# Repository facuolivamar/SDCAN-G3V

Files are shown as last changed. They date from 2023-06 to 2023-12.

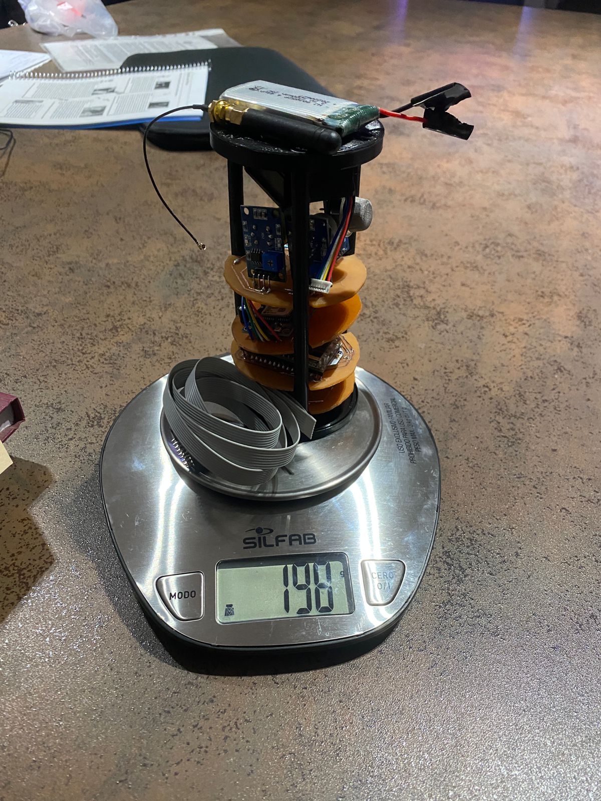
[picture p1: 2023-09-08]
Multimedia/balanza.jpeg

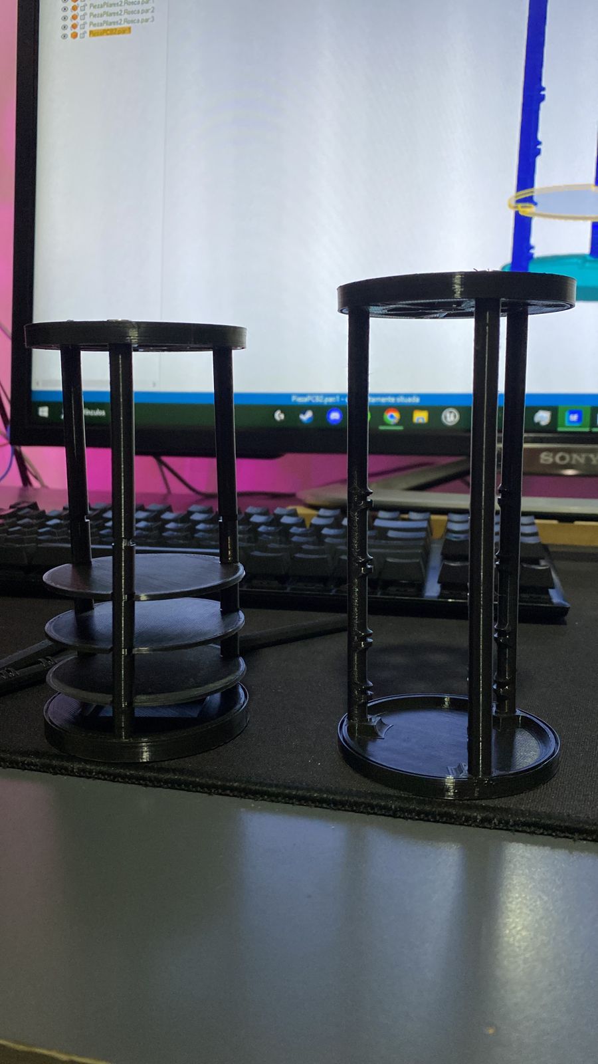
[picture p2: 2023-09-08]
Multimedia/produccion-estructura.jpeg

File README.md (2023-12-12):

# Smog Detector CAN (SDCAN)

## Introduction
This readme provides an overview of the SDCAN project developed by the Equipo Villada para la Investigación Espacial (EVIE) from Instituto Técnico Salesiano Villada. The project aims to measure and monitor air pollution levels in the province of Córdoba, Argentina, using a CanSat (Satellite in a Can) device. The CanSat will collect data on pressure, temperature, ozone levels, nitrogen oxides, volatile organic compounds, carbon dioxide, and particulate matter. The project's primary mission is to transmit this data to a ground station in real-time, while the secondary mission involves studying pollution levels in different areas of the province.

## Mission Name: SDCAN (Smog Detector CAN)
Patch:
Team Organization: Roles
- Luciano Michalik - Teacher Advisor
- Maximiliano Smidt – Structure Designer
- Valentino Velez – Hardware and Firmware Developer
- Facundo Oliva Marchetto – Software Developer
- Mateo Marchisone – Software Developer and Outreach

## Mission Objectives
Primary Mission:
The primary mission consists of sensing pressure and temperature and transmitting this data to the ground station at least once per second. The initial data obtained from measuring pressure and temperature before launch will be used to calculate the CANSAT's altitude, which will be utilized in the secondary mission.

Secondary Mission:
The secondary mission involves studying pollution levels based on the following factors:
- Topography of Córdoba: The city's topography, combined with the phenomenon of thermal inversion, leads to the accumulation of pollutants near the ground, resulting in the formation of a smog cloud.
- Levels of nitrogen oxides in the Province of Córdoba: The high concentration of vehicles and industrial activities, particularly in the automotive and agricultural sectors, contributes to elevated levels of nitrogen oxides (NOx).
- Levels of volatile organic compounds in the Province of Córdoba: Agricultural and livestock activities, along with industrial processes, generate high levels of volatile organic compounds (VOCs) such as methane, toluene, and ethylene.
- Particulate matter 2.5 PM: Fine particulate matter with a diameter of 2.5 microns (PM2.5), originating from various sources, poses health and environmental risks.

The mission aims to measure air quality, NOx levels, VOCs, ozone (O3), and carbon dioxide (CO2) in different areas of the province, including industrial parks and agricultural zones, complementing the existing air quality monitoring stations in the city of Córdoba.

## Preliminary Design
Physical Layout:
The CANSAT's behavior during the mission will follow these steps:
1. While loaded into the rocket before launch, the CANSAT will remain in a dormant state to conserve energy.
2. Once in flight, the CANSAT will start recording all data.
3. Upon ejection, the CANSAT will initiate data transmission while continuing to gather more information.
4. During freefall descent, the parachute will deploy, ensuring a controlled landing.

Subsystems:
- Microprocessor (Computer): The ESP32-LoRa provided by CONAE will be used to store and transmit data, as well as read and process various sensor measurements.
- Communications: The LoRa module integrated into the ESP32 will enable long-range and low-energy data transmission.
- Sensors:
  - Ozone and nitrogen dioxide sensor (MQ131): Used to measure ozone (O3) and nitrogen oxides (NOx) levels.
  - LPG, methane, and carbon monoxide sensor (MQ4): Measures LPG, methane, and CO levels.
  - Air quality sensor (MQ135): Measures CO2, benzene, and toluene levels.
  - GPS module (GY-NEO6MV2): Provides real-time location coordinates.
  - Dust and particle sensor (GP2Y1010AU0F): Measures 2.5 PM particles in the air.
  - NH3 and NO2 sensor (Mics 6814): Measures ammonia and nitrogen dioxide levels.

- Power Unit: A 3.7V, 1200mAh lithium battery will be used as the power source. Voltage regulators (step-up and step-down) will be employed to supply the required voltages (3.3V and 5V) to different components.

## Budget of Mass
The estimated total mass of the CANSAT is 239.45 grams.

## Integration and Testing
The components will undergo preliminary individual testing before the CANSAT assembly. Integration tests will include parachute functionality, descent control, and data transmission. Additionally, the CANSAT will be subjected to simulated conditions such as vacuum and vibration tests to ensure its integrity.

## Documentation and Results
The project's progress will be documented using GitHub for version control. Various documents will outline each stage of the project. Videos and photos will be taken to capture key milestones. Results will be shared through a YouTube channel and an Instagram account dedicated to the project.

GitHub Repository: [Project Repository](https://github.com/facuolivamar/SDCAN-G3V/tree/main)

YouTube Channel: [EVIE SDCAN](https://www.youtube.com/@ITSV-SDCAN)

Instagram Account: [@sdcan_itsv](https://www.instagram.com/sdcan_itsv/)

For a detailed description and visual representation of the project, please refer to the [project video](https://www.youtube.com/watch?v=PZLdEqGG1FY&ab_channel=ITSV-SDCAN).

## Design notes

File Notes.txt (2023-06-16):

Instalar driver para USB
Instalar zip library > SFE_BMP180-master.zip
1. Resistencias
2. Version de la libreria, Version: BPM085 1.0.0
examples >  adafruit BPM085 library > test
examples > WireScan

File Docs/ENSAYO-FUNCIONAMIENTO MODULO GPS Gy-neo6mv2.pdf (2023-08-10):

ENSAYO: Funcionamiento del Módulo GPS Gy-neo6mv2.

En este ensayo, se buscó comprobar el correcto funcionamiento de Módulo GPS Gy-neo6mv2. Para ello, Se utilizo la librería TinyGPS++ y se comprobó que los datos de latitud y longitud que estaba arrojando el sensor sean correctos con la ubicación donde estaba el dispositivo.

Materiales utilizados

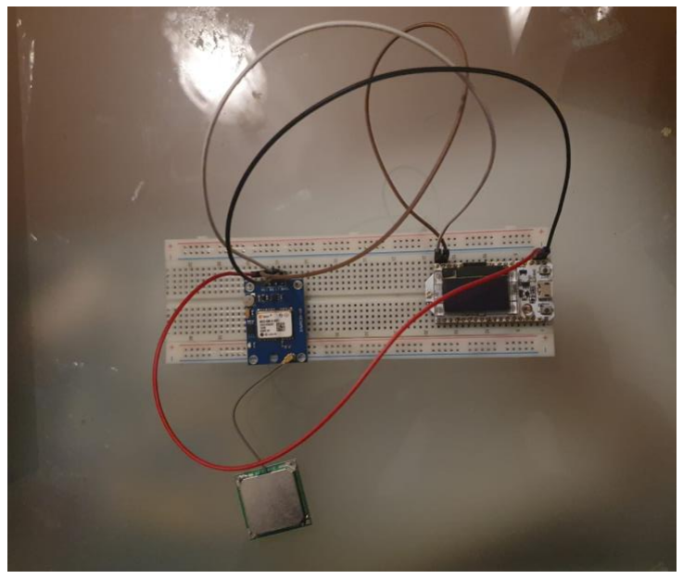
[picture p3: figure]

- WiFi LoRa 32 (V2)
- Módulo GPS Gy-neo6mv2
- Protoboard
- Cables Dupont Macho-Macho

Resultados obtenidos:

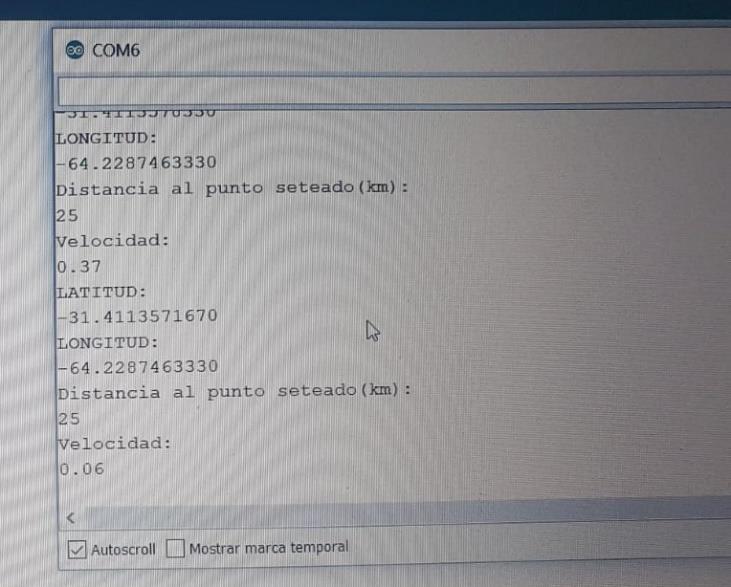
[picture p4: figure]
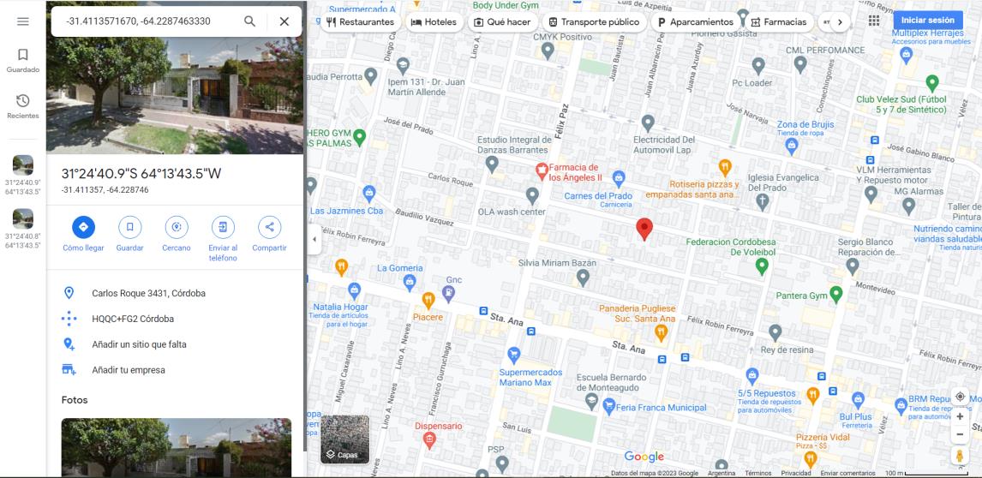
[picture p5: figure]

Los valores de latitud y longitud arrojados por el modulo fueron puestos en Google maps para corroborar que la información que estába dando era correcta.

Conclusiones

- Gracias a los resultados obtenidos se puede preveer el correcto funcionamiento del dispositivo para nuestra misión.

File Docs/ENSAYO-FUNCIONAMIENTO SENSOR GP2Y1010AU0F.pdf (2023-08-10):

ENSAYO: Funcionamiento del Sensor GP2Y1010AU0F

En este ensayo, se busco comprobar el correcto funcionamiento del sensor GP2Y1010AU0F. Para ello, se realizaron pruebas con fósforos con la finalidad de comprobar que el sensor sea capaz de medir la densidad de partículas que desprendían las cerillas al ser apagadas.

Materiales utilizados

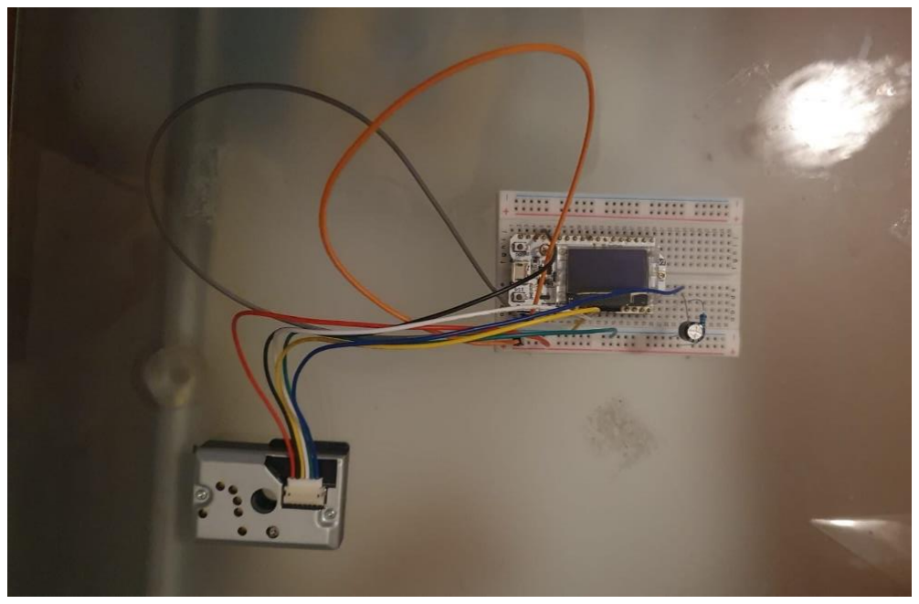
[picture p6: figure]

- WiFi LoRa 32 (V2)
- Sensor GP2Y1010AU0F
- Protoboard
- Resistencia 150 Ω
- Capacitor 220 µF
- Cables Dupont Macho-Macho

Condiciones iniciales:

- Se efectuó 3 testeos en un ambiente cerrado
- Las cerillas fueron apagadas lo más cerca posible del sensor.

Resultados obtenidos:

Conclusiones

- Dado las condiciones del ensayo (ambiente cerrado, sin circulación de aire) se obtuvieron resultados bastantes congruentes entre sí, con una precisión del 1,70%.
- Gracias a los resultados obtenidos se puede preveer el correcto funcionamiento del dispositivo para nuestra misión.
| Valor medio
Valor inicial
| obtenido
(ug/m3)
| (ug/m3)
0 | 2699,00
0 | 2673,00
0 | 2611,00
Precisión | 45,21
Precisión porcentaje | 1,70%

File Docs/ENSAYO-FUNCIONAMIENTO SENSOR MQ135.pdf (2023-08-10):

ENSAYO: Funcionamiento del Sensor MQ135

En este ensayo, se buscó comprobar el correcto funcionamiento del sensor MQ135. Para ello, se realizaron pruebas para corroborar si el sensor MQ135 era capaz de sensar compuestos orgánicos volátiles (benceno, tolueno) siendo útil para nuestra misión. Para ello, se utilizó alcohol y un esmalte de uñas (el esmalte de uñas está compuesto internamente por tolueno)

Materiales utilizados

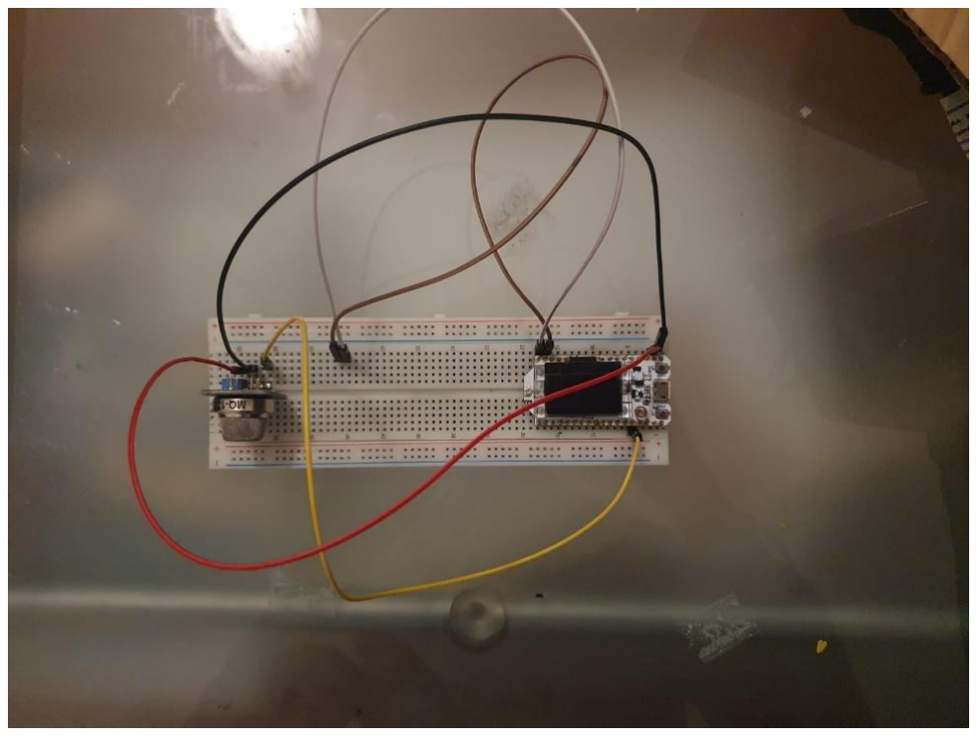
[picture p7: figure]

- WiFi LoRa 32 (V2)
- Sensor MQ135
- Protoboard
- Cables Dupont Macho-Macho

Condiciones iniciales:

- Se efectuó 3 testeos con una tapita llena de alcohol en un ambiente cerrado
- Se efectuó 3 testeos con un esmalte de uñas en un ambiente cerrado.

- El alcohol y el esmalte de uñas fueron puestos lo más cerca posible del sensor

Resultados obtenidos:

Precisión | 10,60
Precisión porcentaje | 12,71%

Conclusiones

- Al ser expuesto al alcohol se obtuvieron resultados bastantes congruentes entre sí, con una precisión del 2,15%.
- Al ser expuesto al esmalte de uñas se obtuvieron resultados bastantes congruentes entre sí, con una precisión del 12,71%.
- Gracias a los resultados obtenidos se puede preveer el correcto funcionamiento del dispositivo para nuestra misión.

Valor inicial alcohol
(ppm)

Valor máx obtenido
despues de 20
segundos expuesto al
alcohol (ppm)
0,09 | 122,28
0,54 | 117,37
0,06 | 121,21
Precisión | 2,58
Precisión porcentaje | 2,15%

Valor inicial tolueno
(ppm)

Valor máx obtenido
despues de 20
segundos expuesto al
tolueno (ppm)
0.10 | 89,42
0.14 | 89,7
0,06 | 71,2

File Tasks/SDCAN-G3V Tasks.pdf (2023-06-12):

Date | Task | Description | Status
23/06/2023 | Primera revisión crítica | Video de la misión primaria, la estructura y el sistema de descenso. Desarrollar sistema para la realizacion de la mision primaria.
23/06/2023 | Estacion espacial | Sensado de presión y temperatura y la transmisión de esos datos a la estación terrena al menos una vez por segundo. (Microprocesador ESP32-LoRa, Sensor MBP180, antena, Batería necesaria, etc)
23/06/2023 | Estacion terrena | Recibir datos de estacion espacial.
23/06/2023 | Interfaz Front-End | Leer desde el puerto serial todos los datos recopilados por el CANSAT y guardar estos datos en un archivo .CSV, además de mostrar valores de interés tales como nivel de batería, posición, etc.
23/06/2023 | Estructura | Estructura en impresion 3D.
23/06/2023 | Sistema de descenso | Paracaídas y electrónica necesaria del mismo. Desarrollar sistema para aterrizaje controlado (GPS, cebos, etc).
23/06/2023 | Video de la mision primaria | Video de funcionamiento de todo lo trabajado en esta primera etapa(mision primaria).

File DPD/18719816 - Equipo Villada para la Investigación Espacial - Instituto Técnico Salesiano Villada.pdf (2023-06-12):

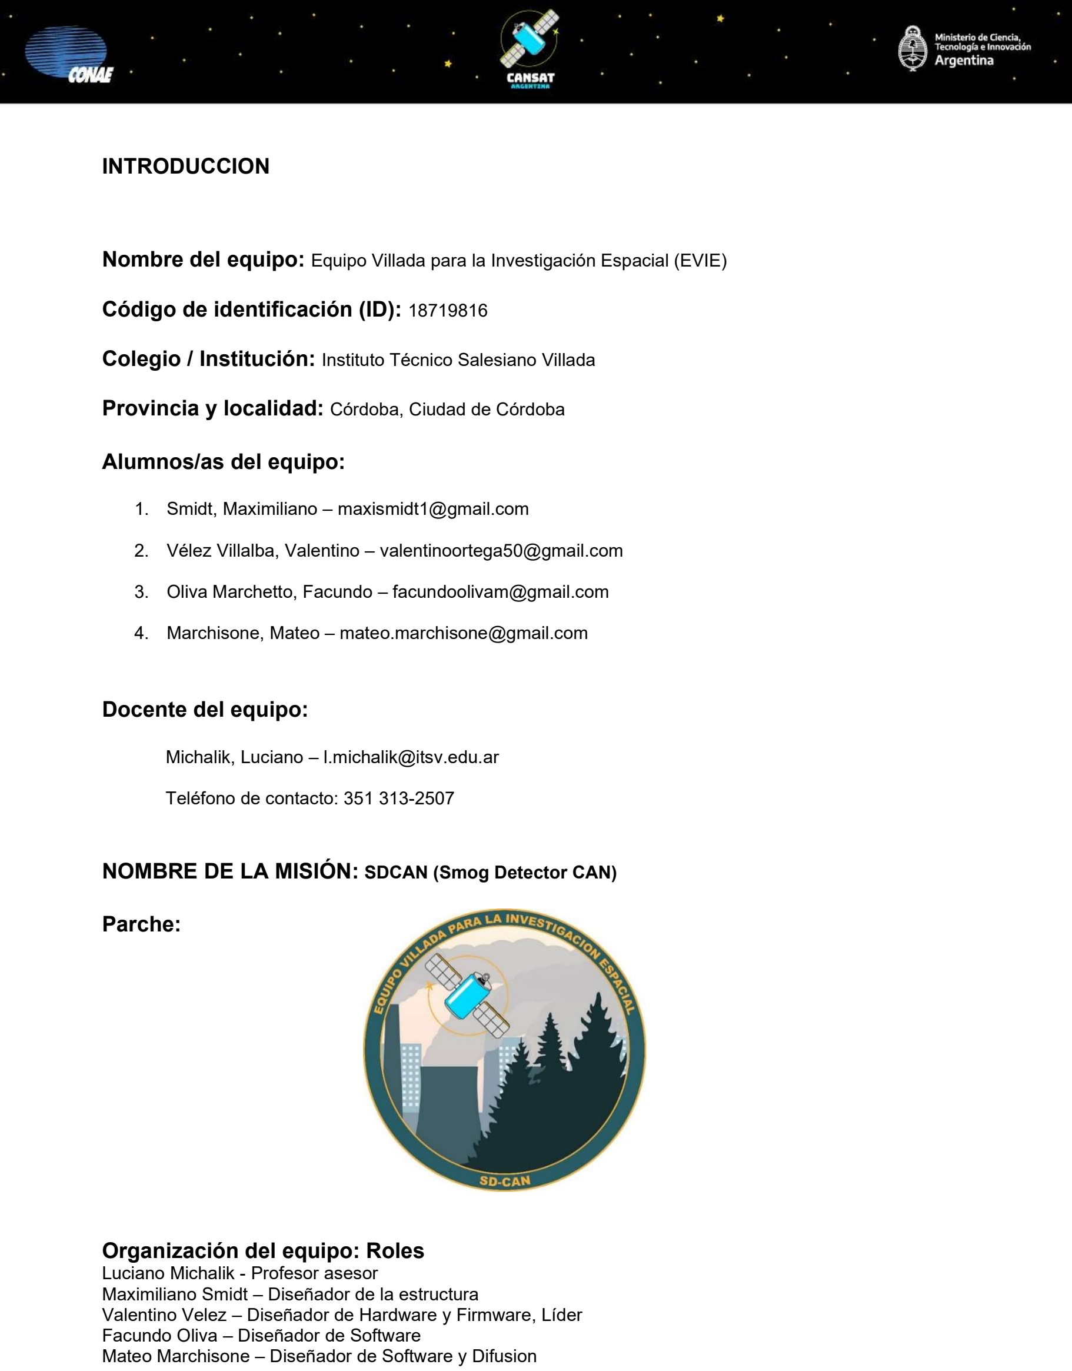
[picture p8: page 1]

### INTRODUCCION

Nombre del equipo: Equipo Villada para la Investigación Espacial (EVIE)

### Código de identificación (ID): 18719816

Colegio / Institución: Instituto Técnico Salesiano Villada

Provincia y localidad: Córdoba, Ciudad de Córdoba

### Alumnos/as del equipo:

### 1. Smidt, Maximiliano – maxismidt1@gmail.com

### 2. Vélez Villalba, Valentino – valentinoortega50@gmail.com

### 3. Oliva Marchetto, Facundo – facundoolivam@gmail.com

### 4. Marchisone, Mateo – mateo.marchisone@gmail.com

### Docente del equipo:

Michalik, Luciano – l.michalik@itsv.edu.ar

Teléfono de contacto: 351 313-2507

NOMBRE DE LA MISIÓN: SDCAN (Smog Detector CAN)

### Parche:

### Organización del equipo: Roles

Luciano Michalik - Profesor asesor
Maximiliano Smidt – Diseñador de la estructura
Valentino Velez – Diseñador de Hardware y Firmware, Líder Facundo Oliva – Diseñador de Software
Mateo Marchisone – Diseñador de Software y Difusion

2

OBJETIVOS DE LA MISIÓN….

### Misión primaria

La misión primaria consiste en el sensado de presión y temperatura y la transmisión de esos datos a la estación terrena al menos una vez por segundo
Para el cálculo de altura del CANSAT, se medirán la presión y temperatura antes del despegue y de esa manera conseguir los datos iniciales necesarios para el cálculo. Este dato lo utilizaremos posteriormente para la misión secundaria

### Misión secundaria

Para la misión secundaria, se realizó un estudio de los niveles de contaminación en base a los siguientes puntos.

### Topografía de Córdoba

En los días de invierno, se produce en la ciudad de Córdoba el fenómeno llamado inversión térmica. Tiene origen en el enfriamiento nocturno del suelo que hace descender la temperatura del aire próximo, que, por ser más pesado, queda estacionado abajo, hasta que, por irradiación solar, se calienta y asciende. Lo que produce la acumulación de contaminantes a pocos metros del suelo y permite que se combinen con la neblina generando así lo que se denomina “nube de smog”
Particularmente dada a la topografía de la ciudad dicho smog es altamente nocivo, ya que la ciudad está en un valle que corre de oeste a este, lo que limita el ‘barrido’ de los vientos norte y sur. Córdoba se ubica en una depresión, por lo cual la circulación y remoción del aire es mucho más lenta.

### Valores de óxidos de nitrógeno en la Provincia de Córdoba

Después de la provincia de Buenos Aires, Córdoba, es la segunda provincia con el mayor número de vehículos en el país (1,49 millones de vehículos)
Industrialmente, Córdoba concentra el 30% de la producción automotriz nacional. En la provincia están instaladas plantas terminales de importantes automotrices mundiales: FCA, Renault, Volkswagen, IVECO y Nissan. Cuenta con una muy desarrollada red de medianas y pequeñas industrias metalmecánicas.
Otro polo industrial es el sector de fabricantes de bienes de capital agrícola, en especial maquinarias y agro componentes.
Además, posee 45 Parques Industriales habilitados, de los cuales, la mayoría están ubicados en la zona sudeste de la región.
Estos factores generan altos niveles de óxidos de nitrógeno, los cuales son unos de los químicos presentes en el smog. Se originan como consecuencia de las combustiones de quemadores, a partir del tráfico y de procesos industriales.

Valores de compuestos orgánicos volátiles en la Provincia de Córdoba.
En temas de agronomía, las principales producciones de Córdoba son las de trigo, maíz, sorgo, soja, girasol y maní.
En actividad ganadera, es la segunda provincia a nivel nacional después de la provincia de Buenos Aires. Su principal producción es el ganado bovino, seguido del porcino, caprino y ovino.
Estos factores generan altos niveles de compuestos orgánicos volátiles (COVs), los cuales son unos de los químicos presentes en el smog. Tienen un origen tanto natural (por el ganado y la agricultura) como antropogénico (debido a la evaporación de disolventes orgánicos, a la quema de combustibles, al transporte, etc.). Si bien hay millones de compuestos que pueden considerarse como COV; los más abundantes son: metano, tolueno, n-butano, i-pentano, etano, benceno, n-pentano, propano y etileno.

### Material particulado 2,5 PM

El material particulado de 2,5 micrones (PM2,5) es tan pequeño que puede inhalarse al respirar y se puede alojar directamente en los pulmones con la posibilidad de que llegue al torrente sanguíneo. Procede de distintas fuentes, en especial por la combustión de combustibles fósiles (tráfico, calefacción, generación de energía), minería, actividades de construcción y demolición o incendios, los cuales pueden generar este tipo de contaminación porque producen partículas livianas que pueden llegar a las ciudades por el viento.

3

Valores del dióxido de carbono en la Provincia de Córdoba.
Además de medir los valores previamente escritos, vamos a medir los niveles de dióxido de carbono (CO2). Las emisiones excesivas de este gas son una de las principales causas del calentamiento global. Un problema causado por la actividad humana, proveniente del consumo energético de los edificios, el transporte y por residuos y cloacas.
Según un dato de la municipalidad del año 2017, la ciudad de Córdoba emite 5,1 millones de toneladas de dióxido de carbono (CO2) al año.

### Daños a la salud y al medioambiente

Algunos de los daños que producen estos contaminantes son:

### 1. Inflamación de las vías respiratorias

2. Tos, dificultad para respirar y opresión en el pecho.
3. Favorece la aparición de enfermedades cardíacas y las agrava.
4. La presencia del smog fotoquímico impide que haya formación de nubes con precipitaciones.
5. Esta capa de contaminación hace que se incrementen las temperaturas por la acumulación excesiva de gases de efecto invernaderos

La misión secundaria consiste en medir los valores de contaminación ambiental de la Provincia de Córdoba. Se medirán la calidad de aire en el lugar, los valores de óxidos de nitrógeno (NOx), compuestos orgánicos volátiles (COVs), Ozono (O3) y Dióxido de carbono (CO2).

Si bien la municipalidad de Córdoba tiene instaladas estaciones para medir la calidad del aire en la ciudad, y publica los reportes anuales en una página web. Nosotros, con la misión SD-CAN proponemos una opción económica y reutilizable que le permita a la municipalidad no solo medir la contaminación ambiental en distintos puntos de la ciudad, sino que también, medirlos en distintas zonas de la provincia, alejadas de la ciudad, como puede ser parques industriales, zonas agrícolas y otros puntos en los cuales se generen mayor cantidad de compuestos químicos contaminantes para el ambiente.

Para el análisis de los datos consideraremos los estándares establecidos por la Agencia de Protección del Medio Ambiente de los Estados Unidos (USEPA). Esta normativa se encuentra en permanente revisión y utiliza valores más estrictos que los enunciados por la Ley Nacional (20.284), que data del año 1973 y nunca fue actualizada.

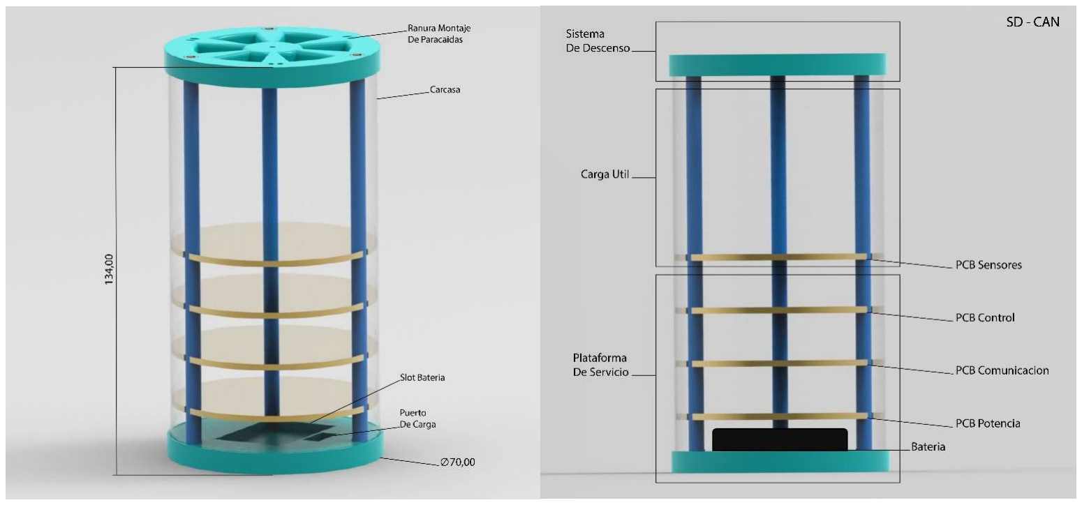
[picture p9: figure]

4

### DISEÑO PRELIMINAR Layout físico

### Como funciona: Operaciones

El comportamiento esperado del CANSAT será el siguiente:
1. Desde que el CANSAT es cargado en el Cohete, y hasta que inicie el lanzamiento, se mantendrá en reposo para ahorrar energía.

### 2. Apenas entre en vuelo, el CANSAT comenzará a registrar toda la información

3. Al momento de la eyección, el CANSAT comenzara la transmisión de datos, mientras paralelamente, sigue almacenando más información..
4. Una vez el CANSAT comienza a descender en caída libre, se abrirá el paracaídas y tendrá un aterrizaje controlado.

### SUBSISTEMAS Microprocesador (computadora)

Utilizaremos el ESP32-LoRa provisto por la CONAE para almacenar y transmitir los datos y realizar las lecturas de las distintas variables a medir para luego procesar esta información y generar los reportes necesarios.

### Comunicaciones

Se utilizará el módulo LoRa contenido por el micro ESP32 provisto por la CONAE. Se transferirá toda la información por este protocolo ya que es de largo rango y consume muy poca energía.

### Sensores

- Sensor de niveles de ozono MQ131: Este sensor permite medir O3 (Ozono), NOx (oxido de nitrogeno). En nuestro caso, lo vamos a utilizar para conocer el nivel de ozono en el aire, el cual es uno de los contaminantes principales del smog.
- Sensor MQ4: Este sensor permite medir LPG (Gas de petroleo), metano, CO (monóxido de carbono). Principalmente, lo vamos a utilizar para medir el LPG y el metano, los cuales son compuestos orgánicos volátiles.
- Sensor de calidad de aire MQ135: Lo vamos a utilizar para medir el CO2 (dióxido de carbono), benceno y tolueno; estos últimos son compuestos orgánicos volátiles.
- Modulo GPS GY-NEO6MV2: Lo vamos a utilizar para saber las coordenadas del CANSAT en todo momento.

5

- Sensor de polvo y partículas GP2Y1010AU0F: Este sensor va a ser utilizado para medir las partículas de 2,5 PM que se encuentran en el aire.
- Mics 6814: vamos a utilizar este sensor para medir los niveles NH3 (Amoniaco) y NO2 (dióxido de nitrogeno), los cuales son los compuestos químicos que el forman a los óxidos de nitrógeno (NOx) Aclaración: Este sensor va a ser importado. En caso de no poder conseguirlo, vamos a utilizar el sensor MQ131 con la calibración correspondiente que permita medir estos compuestos químicos.
- Sensor de Presión y Temperatura: BMP180 Necesario para cumplir la misión designada por CONAE

### Unidad de potencia eléctrica

En nuestro CANSAT poseemos sensores y componentes que su alimentación de entrada es diferente, algunos se deben alimentar con 3,3 V y otros con 5 V. Para la solución de este problema, utilizaremos una batería de Litio de 3,7 V y 1200 mAh que en su salida conectaremos un regulador de voltaje para reducir y estabilizar la tensión a 3,3 V. También conectaremos a la salida de la batería, la fuente step up MT3608 que nos permitirá elevar la tensión obteniendo como resultado una de 5 V. En caso de que la batería de 1200mAh sea insuficiente, una batería alternativa sería una de litio de 3.3v, la cual es más pesada pero posee el doble de capacidad, unos 2400mAh.
A continuación, se presenta un cuadro con los cálculos de la potencia total máxima consumida de los componentes

Para calcular la autonomía de la batería, utilizaremos la siguiente formula:

- Wb: Es el producto entre la tensión de la batería (3,3 V) y la intensidad de la batería (1200 mAh). Esta multiplicación da como resultado 3,960 mW
- Wc: Este resultado lo sacamos de la tabla (3367,5 mW) y representa la potencia total consumida.
- Para calcular cuánto tiempo va a durar la batería, tenemos que dividir los valores previamente calculados (Wb/Wc). Esta división da como resultado que la batería puede durar 1 hora y 17 minutos, tiempo suficiente para poder cumplir y concluir con la misión

### Control de descenso

El control de descenso se basa en el objetivo de hacer que el CANSAT descienda suavemente y sin sufrir daños, mientras este informe sobre su ubicación GPS. Lo haremos a partir de un paracaídas que soporte el peso del mismo, este tendrá 3 puntos de sujeción en la tapa superior. Gracias a la ubicación GPS, sabremos hacia donde se dirige el CANSAT. Esto lo hacemos con la idea de poder recuperar el satélite fácilmente y no sufra daños en el descenso, para que luego podamos reutilizarlo.

### Cálculo de las dimensiones del paracaídas

Para que el tiempo de descenso del CANSAT sea de 85 segundos este debe descender a una velocidad terminal de 3,5 m/s. Para lograr desacelerar la caída libre del CANSAT hasta la velocidad deseada el

Item | Cantidad | Alimentación (V) | Corriente máx (mA) | Potencia máx (mW)
MQ135 | 1 | 5 | 150 | 750
MQ4 | 1 | 5 | 180 | 900
MQ131 | 1 | 5 | 180 | 900
Mics 6814 | 1 | 5 | 30 | 150
ESP32-LoRa | 2 | 3,3 | 50 | 330
BMP 180 | 1 | 5 | 2,5 | 12,5
GP2Y1010AU0F | 1 | 5 | 20 | 100
GY-NEO6MV2 | 1 | 5 | 45 | 225
| Potencia total máxima | | 3367,5
| Corriente total máxima | | 642,5

6

paracaídas utilizado será de forma cóncava y tendrá un radio de 0.26 metros. Estos valores se obtuvieron utilizando la fórmula de velocidad terminal, como se detalla a continuación.

m=Masa del CANSAT
g=Aceleracion de la gravedad
p=Densidad del aire
A=Área proyectada del paracaídas
Cd=Coeficiente de arrastre del paracaídas

### Estructuras

La estructura del CANSAT consiste en una tapa superior y una tapa inferior unidas a través de tres pilares con pequeñas ranuras en las que calzaran las PCBs con los elementos necesarios (todo será construido de impresión 3D). Podremos dividir la estructura en 3 principales grupos.

SISTEMA DE DESCENSO
Ubicado en la parte superior del CANSAT, donde se encuentra el paracaídas encargado de lograr un aterrizaje suave.

CARGA ÚTIL
Ubicado en la parte central del CANSAT, donde se encuentran los sensores principales y los que utilizaremos para medir el SMOG en el ambiente, necesario para cumplir la misión principal y secundaria.

PLATAFORMA DE SERVICIO
Ubicado en la parte inferior del CANSAT, donde se ubicaran todos los sistemas necesarios para el funcionamiento del CANSAT: Control, Comunicación, Potencia y la Batería.
Todo esto será recubierto con una carcasa de aluminio de 0,3mm de espesor, esta tendrá agujeros con un estampado de refuerzo que permiten el flujo de aire y una buena rigidez estructural para lograr una correcta medición de los sensores a bordo en la carga útil y asegurar el CANSAT.

### Software

Programación del Software de Vuelo
Para la programación del software de vuelo, el lenguaje a utilizar,será MicroPython.
MicroPython es una versión de Python que está optimizada para ser utilizada en microcontroladores y dispositivos integrados. Es una excelente opción para programar un ESP32-LoRa porque tiene un tamaño de código pequeño, lo que lo hace ideal para dispositivos con recursos limitados de memoria y almacenamiento, como el ESP32-LoRa.
Al usar MicroPython en el ESP32-LoRa, puedes aprovechar las bibliotecas y módulos de Python existentes. Además, la flexibilidad de Python y la facilidad de depuración y pruebas en el modo interactivo de MicroPython hacen que sea más fácil desarrollar y probar el código en el dispositivo en tiempo real, lo que acelera el proceso de desarrollo.

### Programacion de la estacion terrena

La estación terrena estará equipada con un front-end con una interfaz de usuario que exponga múltiples gráficos sobre variables del CANSAT mismo, y los parámetros a medir, como también estados lógicos. Toda esta información será mostrada de dos formas:
a. Por medio de una computadora
b. Por medio de una transmisión por vía YouTube, con el agregado de una grabación en vivo del lanzamiento.
El software de la estación terrena, desarrollado en Python 3, será capaz de leer desde el puerto serial de la computadora todos los datos recibidos por el módulo LoRa, mostrando a través de una interfaz gráfica todos los datos recopilados por el CANSAT y guardando estos datos en un archivo .CSV, además de mostrar valores de interés tales como nivel de batería, posición, etc. Además, el software será capaz de leer el archivo .CSV guardado en la microSD del CANSAT y convertirlos en un gráfico para su fácil interpretación.

7

### PRESUPUESTO DE MASAS

### PRESUPUESTO

Item | Cantidad | Peso unitario (g) | Subtotal
MQ135 | 1 | 10 | 10
MQ4 | 1 | 10 | 10
MQ131 | 1 | 10 | 10
Mics 6814 | 1 | 2,05 | 2,05
ESP32 -LoRa | 2 | 20 | 40
BMP 180 | 1 | 3 | 3
Bateria 3,7 V | 1 | 24 | 24
MT3608 (Step up) | 1 | 5 | 5
PCB | 4 | 5 | 20
GP2Y1010AU0F | 1 | 16 | 16
GY-NEO6MV2 | 1 | 12 | 12
Paracaidas | 1 | 20 | 20
Tapa Superior | 1 | 15 | 15
Tapa Inferior | 1 | 13 | 13
Pilares Soporte PCB | 3 | 6 | 18
Tornilleria | 1 | 15 | 15
Insertos Roscados | 6 | 0,4 | 2,4
Carcasa Aluminio 0,3 mm | 1 | 4 | 4
| Peso Total | | 239,45

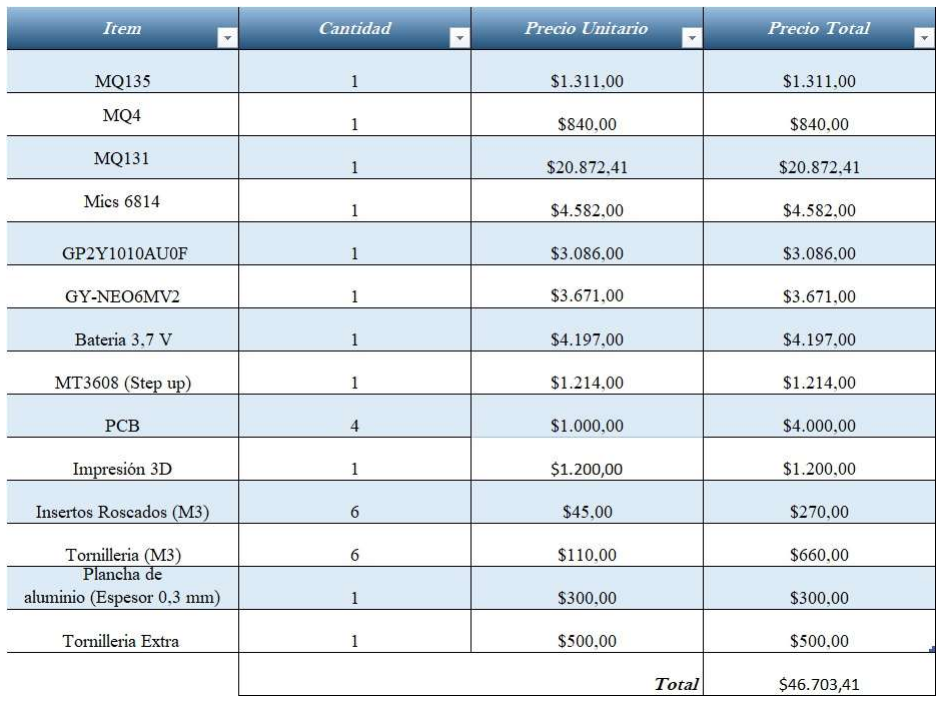
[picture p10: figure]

8

### INTEGRACIÓN Y PRUEBAS Pruebas preliminares de los componentes

Todos los sensores serán testeados individualmente previo al ensamblado del CANSAT en situaciones similares a las condiciones que se pueden presentar una vez que el CANSAT este en el aire.
Para probar el funcionamiento de los módulos LoRA se establecerá un enlace simple entre estos dos y se comprobará el correcto envío y recepción de datos.
Para los sensores MQ se hará la correspondiente “cura” de los sensores, la cual consiste en dejar 24 horas funcionando los sensores antes del primer uso, ya que durante el proceso de fabricación pueden quedar impurezas dentro, que se van a limpiar de esta forma.

### Pruebas de integridad

Para comprobar la integridad del CANSAT, Se lo lanzara desde distintas alturas y con distintas velocidades para corroborar el correcto funcionamiento del paracaídas y permita un descenso controlado.
Buscaremos algunas maneras de probar el CANSAT en condiciones lo más similares posibles a las condiciones que existirán durante la misión, sometiéndolo a pruebas de vacío y vibraciones. También, vamos a sujetar el CANSAT en un dron para así poder comprobar el correcto funcionamiento de la carga útil a diferentes alturas.

### Plan de validación (medidas, peso, integridad, tests ambientales)

Para validar que el peso de nuestro CANSAT este adentro de los requerimientos de la CONAE utilizaremos una balanza de precisión
Para validar que el tamaño de nuestro CANSAT este adentro de los requerimientos de la CONAE utilizaremos herramientas de medición y fabricaremos un cilindro cuyas dimensiones sean las máximas permitidas, y nos aseguraremos de que nuestro CANSAT pueda entrar correctamente dentro de este cilindro.

9

### CAPACIDADES

Facundo Oliva cuenta con el 1er puesto en las ONIET 2022 en la disciplina de DESARROLLO DE SISTEMAS.

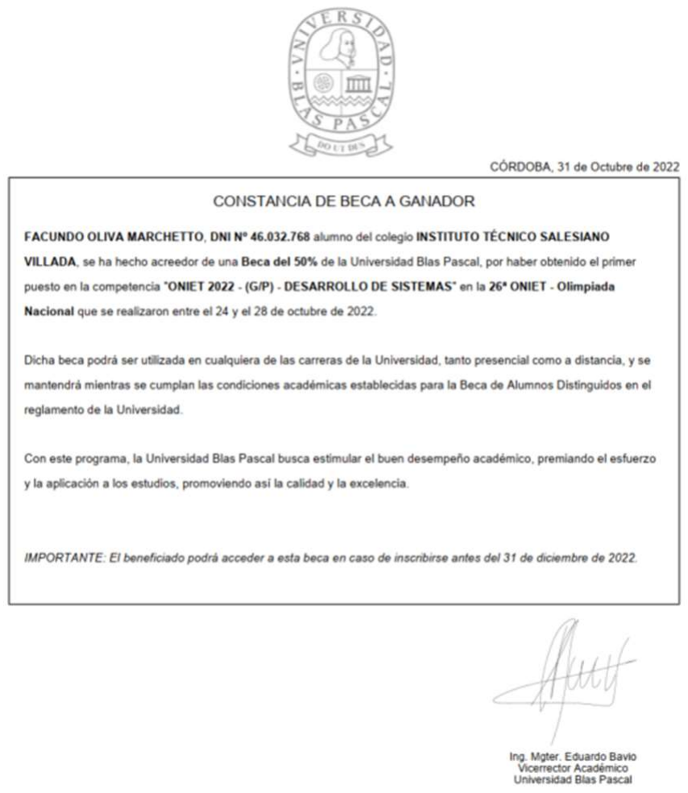
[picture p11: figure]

Mateo Marchisone cuenta con el 2do puesto en las ONIET 2022 en la disciplina de DESARROLLO DE SISTEMAS.

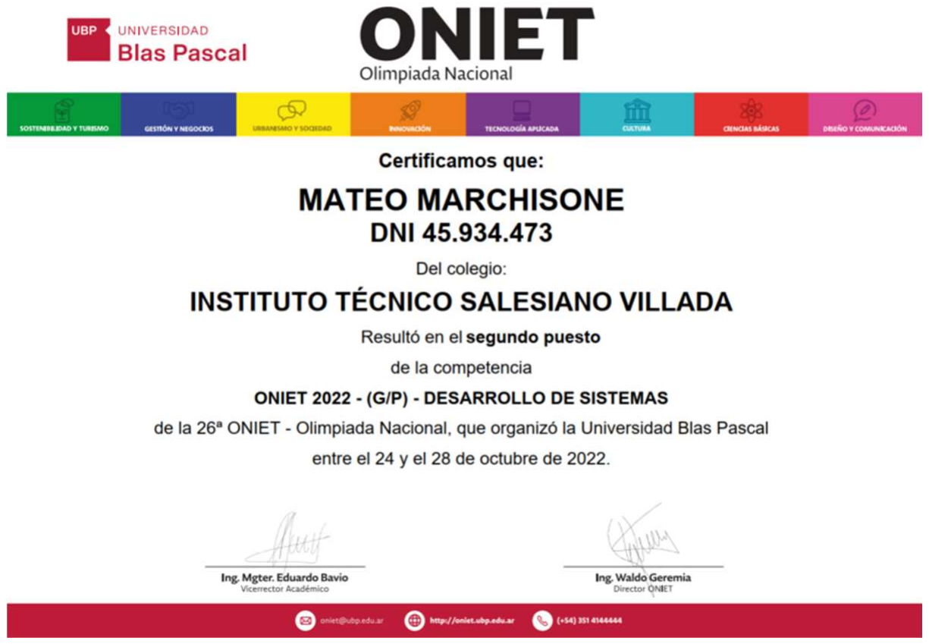
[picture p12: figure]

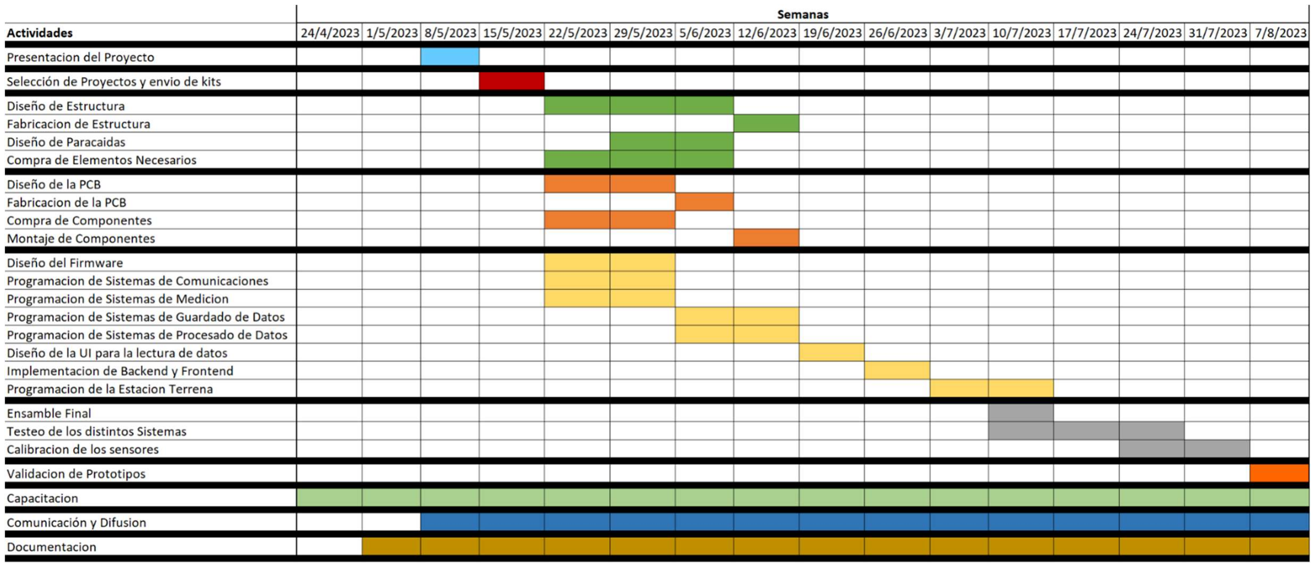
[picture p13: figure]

10

### AGENDA

### PLAN DE DOCUMENTACIÓN

El proceso se registrará en un conjunto de documentos que van a explicar con detalle lo que se hará en cada etapa. Se utilizará Github para el versionado de las diferentes versiones de software (satélite, estación terrena, análisis de datos, firmware,etc). También se grabarán pequeños videos y tomarán fotos del proceso y resultado de las determinadas etapas o tareas a cumplir.

### PLAN DE PUBLICACIÓN Y DIFUSIÓN DE RESULTADOS

Se contará con un canal de Youtube en el que se subirán diversos videos, principalmente del proceso y de hitos cumplidos del proyecto. También se contará con una cuenta de Instagram para realizar publicaciones del proceso más frecuentemente.

Canal de Youtube: https://www.youtube.com/@ITSV-SDCAN
Cuenta de Instagram: https://www.instagram.com/sdcan_itsv/

### Link al VIDEO

https://www.youtube.com/watch?v=PZLdEqGG1FY&ab_channel=ITSV-SDCAN

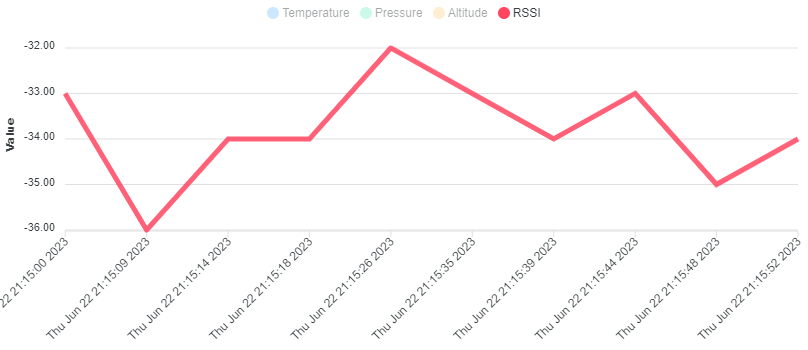
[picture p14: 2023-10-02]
Math/18bci3m4.png

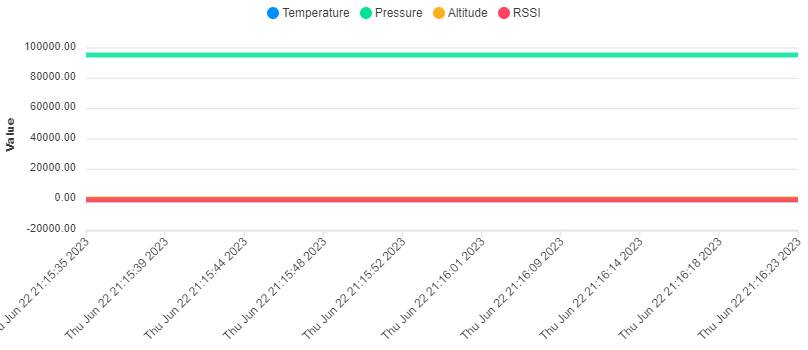
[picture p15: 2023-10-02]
Math/18bci3m4 (1).png

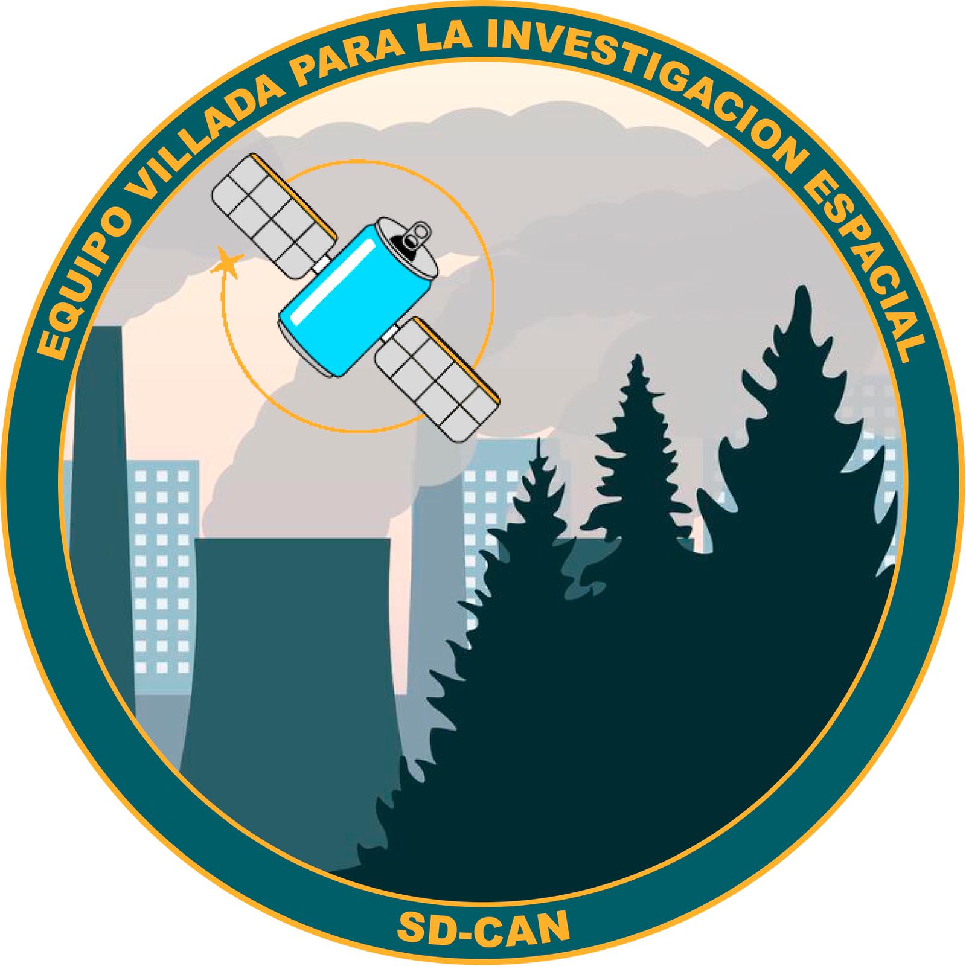
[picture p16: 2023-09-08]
Multimedia/parche.jpeg

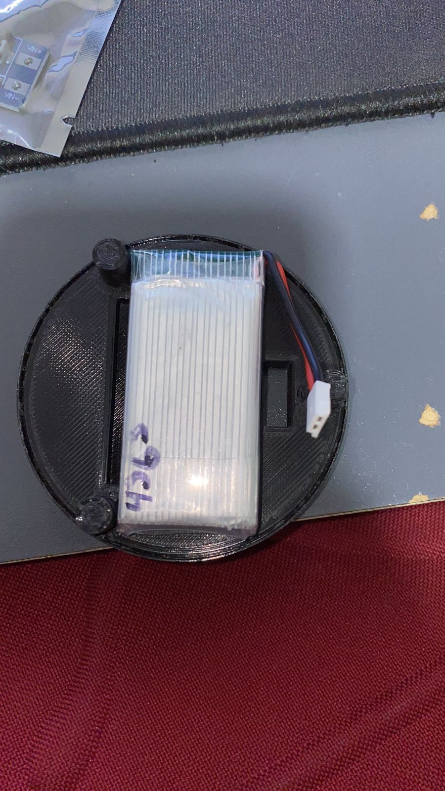
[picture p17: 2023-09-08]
Multimedia/estructura-batería-2023-07-26.jpeg

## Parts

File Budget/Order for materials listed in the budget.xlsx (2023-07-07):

Product | Link | Quantity | Status | Unit Price | Extras | Total cost | Check
MQ135 | Sensor De Gas Mq135 Nh3 Nox Co2 Alcohol Benzeno Humo – Candy-HO (https://candy-ho.com/producto/sensor-de-gas-mq135-nh3-nox-co2-alcohol-benzeno-humo/) | 1 | Recibido | 1508 |  | 1508 | TRUE
MQ4 | Sensor MQ4 (https://candy-ho.com/producto/modulo-detector-sensor-mq4-gas-natural-metano-arduino/) | 1 | Recibido | 731 |  | 2239 | TRUE
Gp2y1010au0f | Sensor de polvo (https://candy-ho.com/producto/modulo-sensor-optico-de-polvo-sharp-gp2y1010au0f-arduino-arm/) | 1 | Recibido | 2046 |  | 4285 | TRUE
Gps Gy-neo6mv2 | Modulo GPS (https://candy-ho.com/producto/modulo-gps-gy-neo6mv2-con-antena-arduino-pic-avr-raspberry/) | 1 | Recibido | 3552 |  | 7837.00 | TRUE
Batería 3.7v 1200mah | Bateria (https://candy-ho.com/producto/bateria-litio-polimero-lipo-3-7v-1200mah-drones-helicopteros/) | 1 | Recibido | 4965 | 3292.16 | 16094.16 | TRUE
MQ131 | Sensor de ozono MQ131 (https://articulo.mercadolibre.com.ar/MLA-882573581-sensor-mq131-gas-ozono-sanitizacion-mq-131-_JM) | 1 | En camino | 22120 |  | 38214.16 | FALSE
Modulo cargador TP4056 | Vendedor (Cordoba) | 1 | - | 600 | 0 | 38814.16 | FALSE
Fuente Step-Up MT3608 | Vendedor (Cordoba) | 1 | - | 800 | 0 | 39614.16 | FALSE

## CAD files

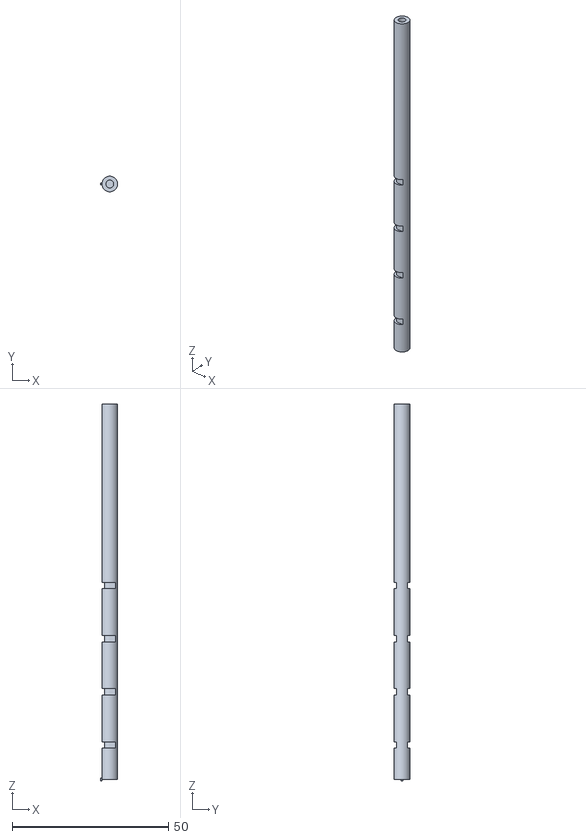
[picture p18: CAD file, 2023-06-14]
3D printing/PiezaPilares2.Rosca.Perfecto.stl
5.50 x 5.00 x 120.5

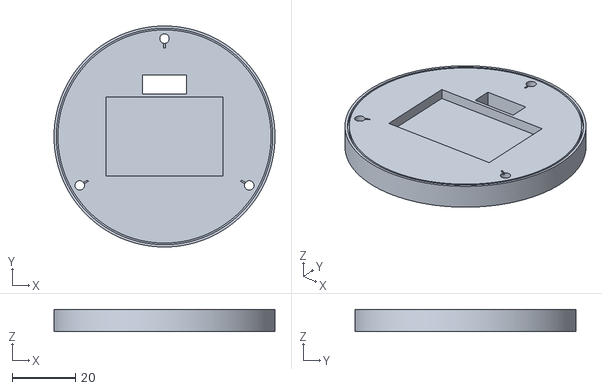
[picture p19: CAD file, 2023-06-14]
3D printing/PiezaTapaInferior1.Perfecto.stl
70.0 x 70.0 x 7.00

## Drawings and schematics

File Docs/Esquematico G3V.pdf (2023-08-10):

## USB

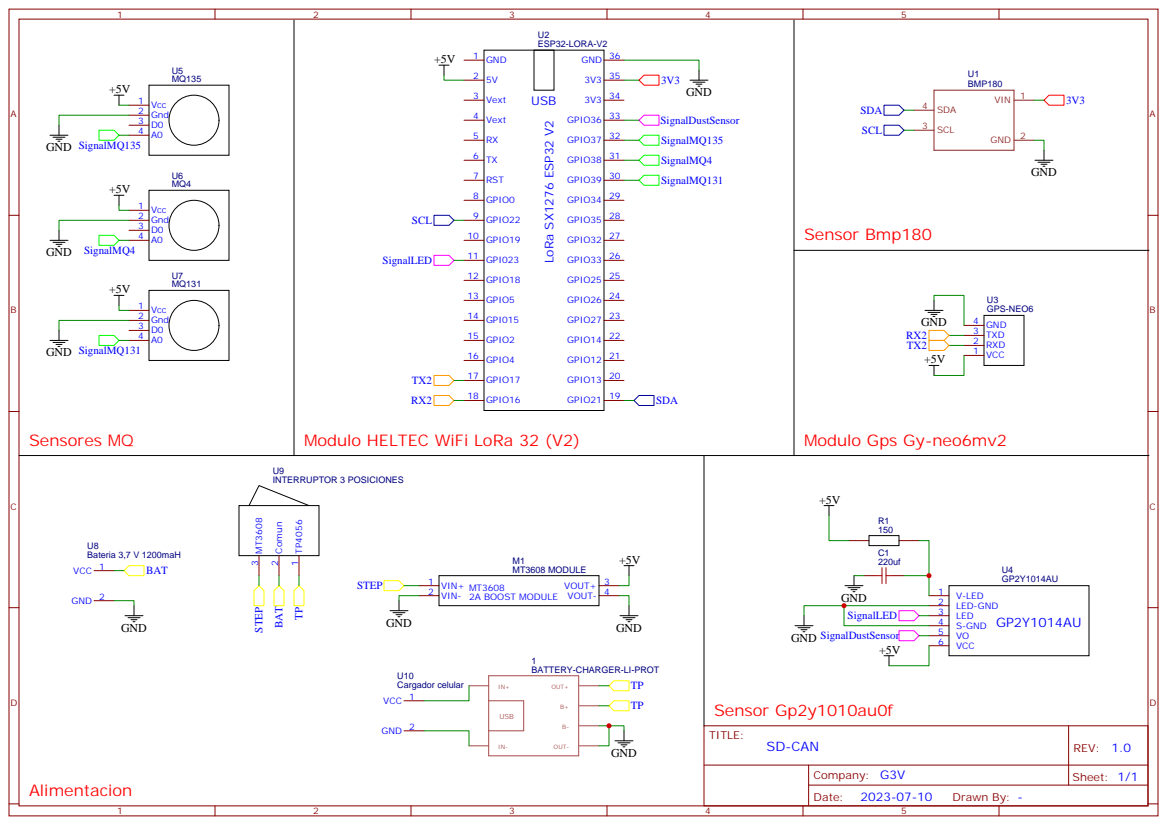
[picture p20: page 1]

BATTERY-CHARGER-LI-PROT

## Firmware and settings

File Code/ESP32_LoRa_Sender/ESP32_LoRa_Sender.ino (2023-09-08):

#include <SPI.h>
#include <LoRa.h>
#include <Wire.h>
#include <Adafruit_BMP085.h>
#include <MQUnifiedsensor.h>
#include <TinyGPS++.h>

//define the pins used by the transceiver module
#define ss 18
#define rst 14
#define dio0 26

#define RXD2 16
#define TXD2 17
HardwareSerial neogps(2);
TinyGPSPlus gps;

int counter = 0;
Adafruit_BMP085 bmp;

#define Board ("LoRa ESP32")
#define Voltage_Resolution (3.3)
#define ADC_Bit_Resolution (12)


//MQ4
#define Type_MQ4 ("MQ-4")
#define RatioMQ4CleanAir (4.4)
#define Pin_MQ4 (38)
MQUnifiedsensor MQ4(Board, Voltage_Resolution, ADC_Bit_Resolution, Pin_MQ4, Type_MQ4);


//MQ131
#define Pin_MQ131 (39)                 
#define Type_MQ131 ("MQ-131")          
#define RatioMQ131CleanAir (15)  
MQUnifiedsensor MQ131(Board, Voltage_Resolution, ADC_Bit_Resolution, Pin_MQ131, Type_MQ131);


//MQ135
#define Pin_MQ135 (37)                 
#define Type_MQ135 ("MQ-135")          
#define RatioMQ135CleanAir (3.6)       
MQUnifiedsensor MQ135(Board, Voltage_Resolution, ADC_Bit_Resolution, Pin_MQ135, Type_MQ135);


void setup() {
  //initialize Serial Monitor
  Serial.begin(115200);
  Serial.println();
  Serial.println();
  
  // neogps.begin(115200, SERIAL_8N1, RXD2, TXD2);

  MQ4.setRegressionMethod(1);
  MQ4.init();

  MQ131.setRegressionMethod(1);
  MQ131.setA(23.943);
  MQ131.setB(-1.11);
  MQ131.init();

  MQ135.setRegressionMethod(1);
  MQ135.init();

  // Setups and Calibrates MQ4
  setUpAndCalibrateMQ4();

  // Setups and Calibrates MQ131
  setUpAndCalibrateMQ131();

  // Setups and Calibrates MQ135
  setUpAndCalibrateMQ135();

  // Setup LoRa
  setUpLoRa();

  // Check BMP
  checkBMP();


}

void loop() {
  Serial.print("Sending packet: ");
  Serial.println(counter);

  //Send LoRa packet to receiver
  LoRa.beginPacket();

  printValue("Packet", counter, "");


  printValue("Temperature", bmp.readTemperature(), "°C");
  printValue("Pressure", bmp.readPressure(), "Pa");
  printValue("Altitude", bmp.readAltitude(), "meters");


  MQ4.update();
  printValue("LPG", readLiquidPetrolGas(), "");
  printValue("CH4", readMethane(), "");

  MQ131.update();
  printValue("O3", MQ131.readSensor(), "");

  MQ135.update();
  printValue("CO", readCarbonMonoxide(), "");
  printValue("CO2", readCarbonDioxide(), "");
  printValue("NH4", readAmmonium(), "");
  printValue("Toluen", readToluen(), "");

  // Get locatioan and speed
  //getLocationAndSpeed();

  LoRa.endPacket();

  counter++;

  delay(10);
}


void setUpAndCalibrateMQ4() {
  Serial.print("Calibrating MQ4 please wait.");
  float calcR0 = 0;
  for (int i = 1; i <= 10; i++) {
    MQ4.update();  // Update data, the arduino will read the voltage from the analog pin
    calcR0 += MQ4.calibrate(RatioMQ4CleanAir);
    Serial.print(".");
  }
  MQ4.setR0(calcR0 / 10);
  Serial.println("  done!.");

  if (isinf(calcR0)) {
    Serial.println("Warning: Conection issue, R0 is infinite (Open circuit detected) please check your wiring and supply");
    while (1)
      ;
  }
  if (calcR0 == 0) {
    Serial.println("Warning: Conection issue found, R0 is zero (Analog pin shorts to ground) please check your wiring and supply");
    while (1)
      ;
  }
}

void setUpAndCalibrateMQ131() {
  Serial.print("Calibrating MQ131 please wait.");
  float calcR0 = 0;
  for (int i = 1; i <= 10; i++) {
    MQ131.update();  // Update data, the arduino will read the voltage from the analog pin
    calcR0 += MQ131.calibrate(RatioMQ131CleanAir);
    Serial.print(".");
  }
  MQ131.setR0(calcR0 / 10);
  Serial.println("  done!.");

  if (isinf(calcR0)) {
    Serial.println("Warning: Conection issue, R0 is infinite (Open circuit detected) please check your wiring and supply");
    while (1)
      ;
  }
  if (calcR0 == 0) {
    Serial.println("Warning: Conection issue found, R0 is zero (Analog pin shorts to ground) please check your wiring and supply");
    while (1)
      ;
  }
}

void setUpAndCalibrateMQ135() {
  Serial.print("Calibrating MQ135 please wait.");
  float calcR0 = 0;
  for (int i = 1; i <= 10; i++) {
    MQ135.update();  // Update data, the arduino will read the voltage from the analog pin
    calcR0 += MQ135.calibrate(RatioMQ135CleanAir);
    Serial.print(".");
  }
  MQ135.setR0(calcR0 / 10);
  Serial.println("  done!.");

  if (isinf(calcR0)) {
    Serial.println("Warning: Conection issue, R0 is infinite (Open circuit detected) please check your wiring and supply");
    while (1)
      ;
  }
  if (calcR0 == 0) {
    Serial.println("Warning: Conection issue found, R0 is zero (Analog pin shorts to ground) please check your wiring and supply");
    while (1)
      ;
  }
}

void setUpLoRa() {
  while (!Serial)
    ;
  Serial.println("LoRa Sender");
  LoRa.setPins(ss, rst, dio0);

  while (!LoRa.begin(865.0625E6)) {
    Serial.println(".");
    delay(500);
  }

  LoRa.setSyncWord(0xF3);
  Serial.println("LoRa Initializing OK!");
}


void checkBMP() {
  if (!bmp.begin()) {
    Serial.println("Could not find a valid BMP085 sensor, check wiring!");
    while (1) {}
  }
}



void printValue(char* valueName, double value, char* unit) {
  LoRa.print("- ");
  LoRa.print(valueName);
  LoRa.print(": ");
  LoRa.print(value);
  LoRa.print(" ");
  LoRa.print(unit);
  LoRa.print("\n");
}

float readLiquidPetrolGas() {
  return readMQ4(3811.9, -3.113);
}

float readMethane() {
  return readMQ4(1012.7, -2.786);
}

float readCarbonMonoxide() {
  return readMQ135(605.18, -3.937);
}

float readCarbonDioxide() {
  return readMQ135(110.47, -2.862);
}

float readAmmonium() {
  return readMQ135(102.2, -2.473);
}

float readToluen() {
  return readMQ135(44.947, -3.445);
}

float readMQ4(float a, float b) {
  MQ4.setA(a);
  MQ4.setB(b);
  return MQ4.readSensor();
}

float readMQ135(float a, float b) {
  MQ135.setA(a);
  MQ135.setB(b);
  return MQ135.readSensor();
}

void getLocationAndSpeed() {

  boolean Data = false;
  for (unsigned long start = millis(); millis() - start < 1000;) {
    while (neogps.available()) {
      if (gps.encode(neogps.read())) {
        Data = true;
      }
    }
  }

  if (Data == true) {
    Data = false;

    if (gps.location.isValid() == 1) {

      printLocation();

      if (gps.speed.isValid() == 1) {
        printValue("Speed", gps.speed.kmph(), "km/h");
      }

    } else {
      printValue("No Data", 404, "");
    }
  }
}

void printLocation() {
  LoRa.print("- Latitude: ");
  LoRa.print(gps.location.lat(), 10);
  LoRa.print("\n");
  LoRa.print("- Longitude: ");
  LoRa.print(gps.location.lng(), 10);
  LoRa.print("\n");
}

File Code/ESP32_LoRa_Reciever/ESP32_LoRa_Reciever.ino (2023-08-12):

#include <SPI.h>
#include <LoRa.h>

//define the pins used by the transceiver module
#define ss 18
#define rst 14
#define dio0 26

void setup() {
  //initialize Serial Monitor
  Serial.begin(115200);
  while (!Serial)
    ;
  Serial.println("LoRa Receiver");

  //setup LoRa transceiver module
  LoRa.setPins(ss, rst, dio0);

  //replace the LoRa.begin(---E-) argument with your location's frequency
  while (!LoRa.begin(865.0625E6)) {
    Serial.println(".");
    delay(500);
  }

  // Change sync word (0xF3) to match the receiver
  // The sync word assures you don't get LoRa messages from other LoRa transceivers
  // ranges from 0-0xFF
  LoRa.setSyncWord(0xF3);
  Serial.println("LoRa Initializing OK!");
}

void loop() {
  // try to parse packet
  int packetSize = LoRa.parsePacket();
  if (packetSize) {
    // received a packet


    // read packet
    while (LoRa.available()) {
      String LoRaData = LoRa.readString();
      Serial.print(LoRaData);
    }

    // print RSSI of packet
    Serial.print("\n- RSSI: ");
    Serial.println(LoRa.packetRssi());
    Serial.print("---------- \n");
  }
}

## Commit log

2023-06-14 3D printing
    [PiezaPilares2.Rosca.Perfecto.stl, PiezaTapaInferior1.Perfecto.stl]
2023-06-15 Moved WireScan folder to Code folder
2023-06-19 data storage 1st steps.
    [data.csv]
2023-06-21 Updating new values and its index.
    [machine-readable-business-employment-data-mar-2023-quarter.csv]
2023-06-21 Math calculations.
    [paracaidas.xlsx]
2023-06-22 storing new serial data
    [data-receiver.csv, data.csv]
2023-06-22 Updated customers.py to storage serial monitor data. It remains to fix some errors.
    [consumers.py]
2023-06-22 fixed errors + modified sleep time
    [consumers.py]
2023-06-22 data to practice.
    [data-receiver.csv]
2023-06-22 comented: chatSocket.onopen and send_initial_data. Uncomment to use the server if the components are not connected to the computer, for testing purposes only (comment out the csv_data_storage functio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
    [data-receiver.csv]
2023-07-07 Renamed Tasks folder. New Budget folder. Added data-receiver file for testing purposes.
    [Order for materials listed in the budget.xlsx, data-receiver.csv, machine-readable-business-employment-data-mar-2023-quarter.csv]
2023-07-27 All sensors working
2023-08-12 new data structure in csv
    [data-receiver-old.csv, data-receiver.csv]
2023-08-12 toluen to toluene
    [data-receiver.csv]
2023-09-27 patterns recognize working
    [data-receiver-150ms.csv]
2023-09-27 data to csv
    [data-receiver-150ms.csv]
2023-09-28 directory + non used files
    [data-receiver-150ms.csv, data-receiver-150ms.xlsx, data-receiver-old.csv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]
2023-09-28 read_csv bad lines fixed
    [consumers.py]
2023-09-30 removed unused folders
    [data-receiver-150ms.csv]
2023-10-02 data lanzamiento 02/10/23
    [data-receiver-150ms.csv]
